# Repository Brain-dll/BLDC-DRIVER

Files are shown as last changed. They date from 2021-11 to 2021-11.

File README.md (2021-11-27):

# BLDC-DRIVER

## INTRODUCTION
BLDC-DRIVER is usually uses for driving brusless DC motor. The brusless DC motor has three input, these inputs connect to coils. Rotor of the motor has permenant magnet, 
When inputs are energized, a temporary magnetism is occurred interaction between permanent and temporary magnets poles. As half bridge and full bridge can be designed two type of 
driver. These drivers work at the same principle but there is a difference between them . Full bridge driver can connect a coil to battery and other coil to ground at the same time. 
Thus system can be more efficient. But Half bridge driver can connect just one coil to battery or ground at the same time. You can observe difference of half and full bridge driver 
designs at below picture:

**HALF BRIDGE DRIVER**



**FULL BRIDGE DRIVER**

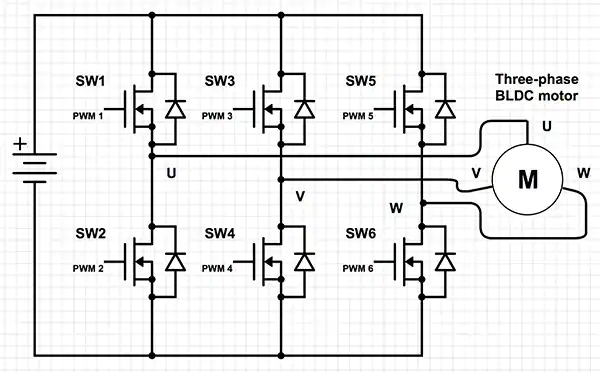
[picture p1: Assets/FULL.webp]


The problem with BLDC drivers is that they don't know the right moment of energizing. To understand when the energizing sequence changes, we must know the rotor current position firstly.
There are two way for determining current rotor position. First one is traditional technic which uses hall effect sensors. According to sensors output, driver can understand current 
moment of changing. To use extra sensors can increase motors cost, connection number and volume. So this makes our boards more complex. Second way is EMF technic. Stator coil has 
star connection, total voltage level of junction point of these coils always have to be zero. According to below picture, When rotor turns around itself total magnetic field of 
star connection be forced to stay at zero. If you observe graph of EMF and sum of magnetic fields, you can see total magnetic flux is zero. We can call common point of coils as virtual 
zero. According to EMF graph, we can understand that magnets come to middle of the two coils, when unenergized coil cross the virtual zero. Thus we can detect correct moment for 
energizing next coil. For example, when A input be charged and B input is uncharged, C input will be inducted with energy and due to motion, the pole of energy will be changed. Thus 
the energy of C input crosses the virtual zero limit. This level-changing event will be followed by the controller. When this event occurs, the ISR goes into propagation and the energizing 
order is changed.

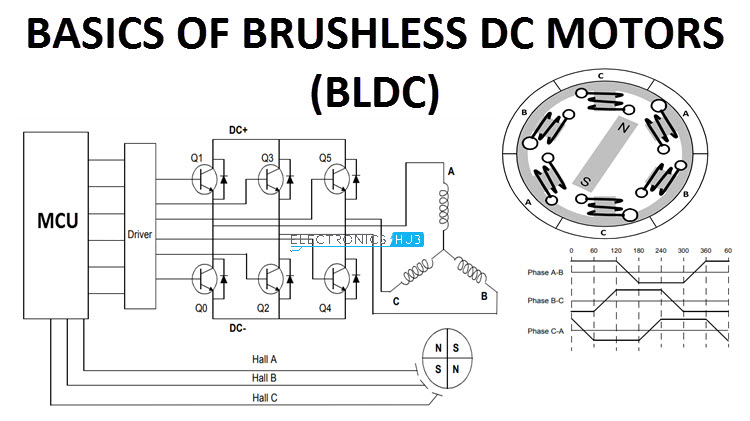
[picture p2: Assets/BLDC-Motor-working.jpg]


Above diagram show full bridge driver structure. Purpose of this project is designing our own a full bridge motor driver and developing drive algorithms at commercial driver level. 
Actually, this project is first step of the orginal drone project. This project was planned as two variant, one of them is a bit bigger than other one. Controllers of variants can 
be different and some components will be able to change. Both of variants will be produced and tested.

## ATMEGA88PA VARIANT
ATMEGA88PA is controller which was produced by microchip company. It is cheap, easily findable and It includes programmable comparator. Thanks to programmable comparator, more space 
can be earned at the board. Flash memory has less space so we can better program it without bootloader. We can earn more memory as programming at register level.

### Components

* ATMEGA88PA Controller
* TC427COA Mosfet Driver
* IRLR7843TRPBF Mosfet
* Other passive components

**Warning : Mosfet driver has to be noninverting, Inverting drivers has PMOS technology so It's working prenciple is vice versa.**

Our schematic design consist of two page. First of them includes controller design and second one includes mosfets, drivers and connectors

**First Page:**

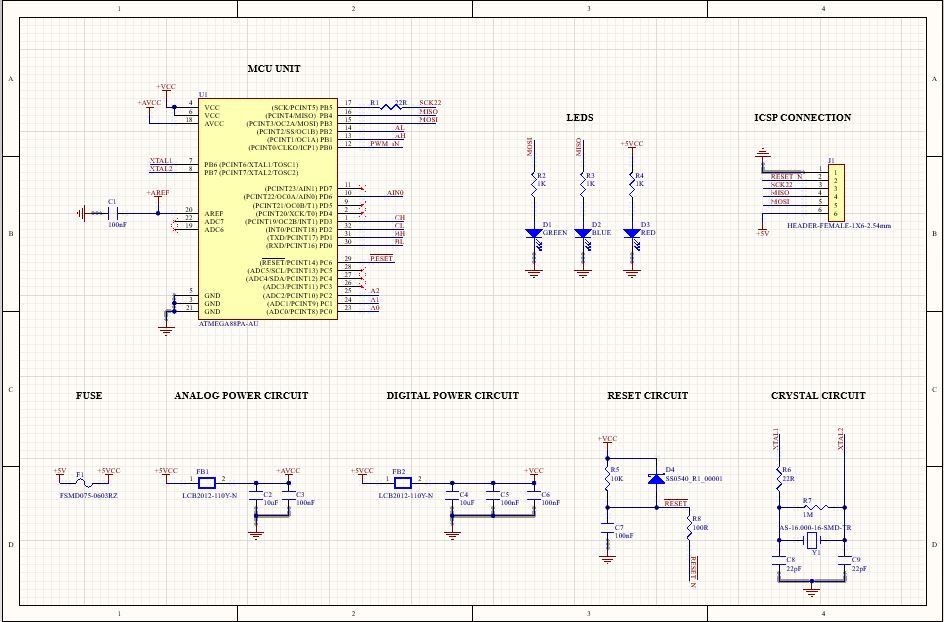
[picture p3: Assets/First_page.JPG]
First_page


**Second Page:**

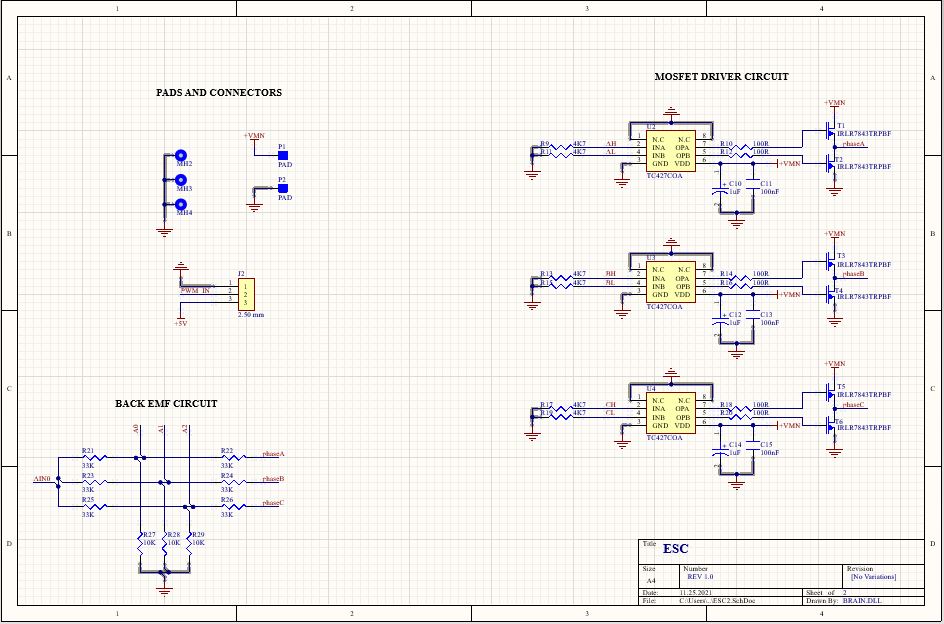
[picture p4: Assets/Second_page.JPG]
Second_page


As you can see, some resistors combination was built, purpose of this combination is taking acceptable feedback from driver (for back EMF).

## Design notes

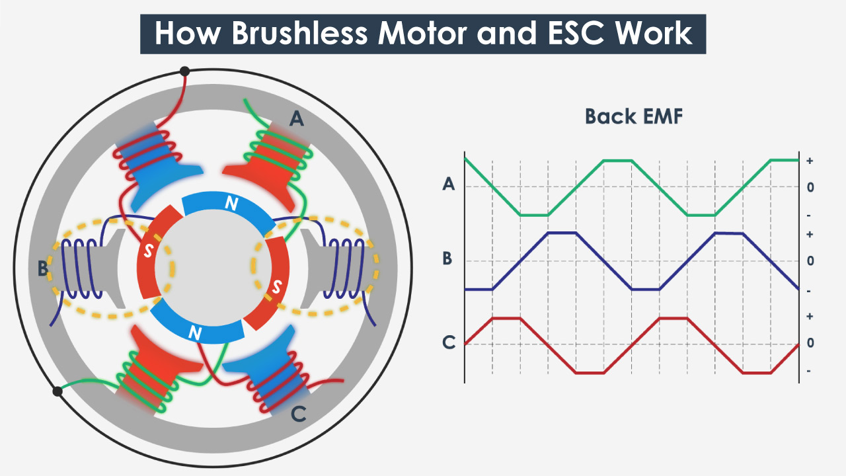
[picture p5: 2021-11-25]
Assets/ESC-Work.jpg

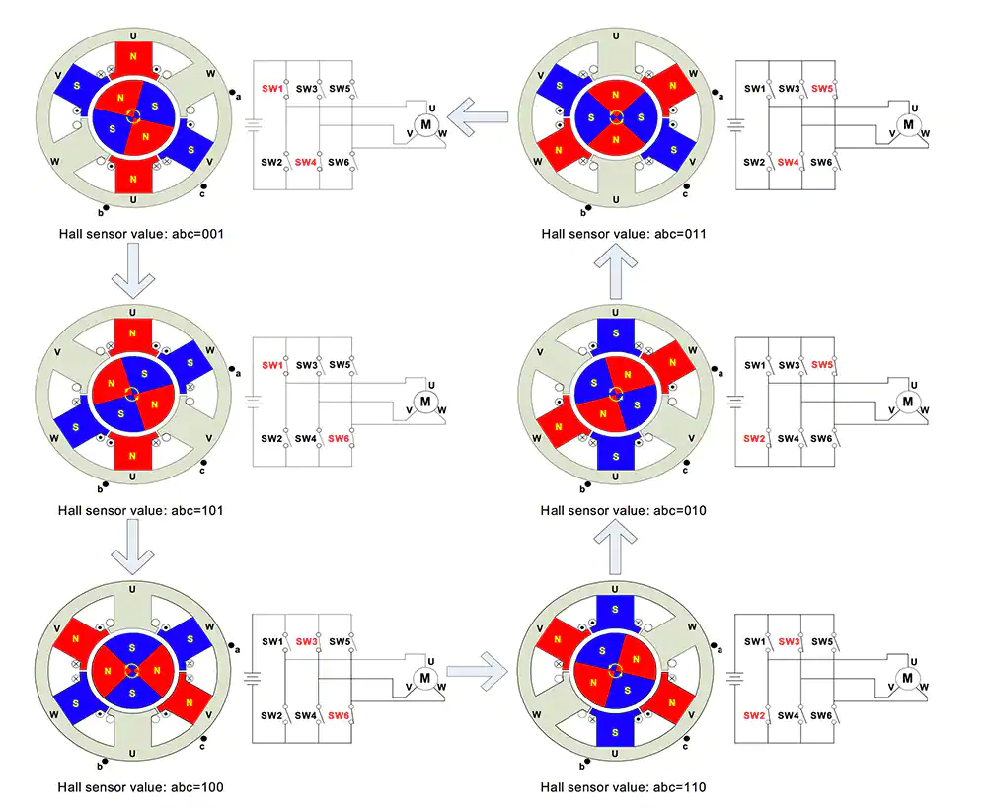
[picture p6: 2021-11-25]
Assets/BLDC_TURNING.webp

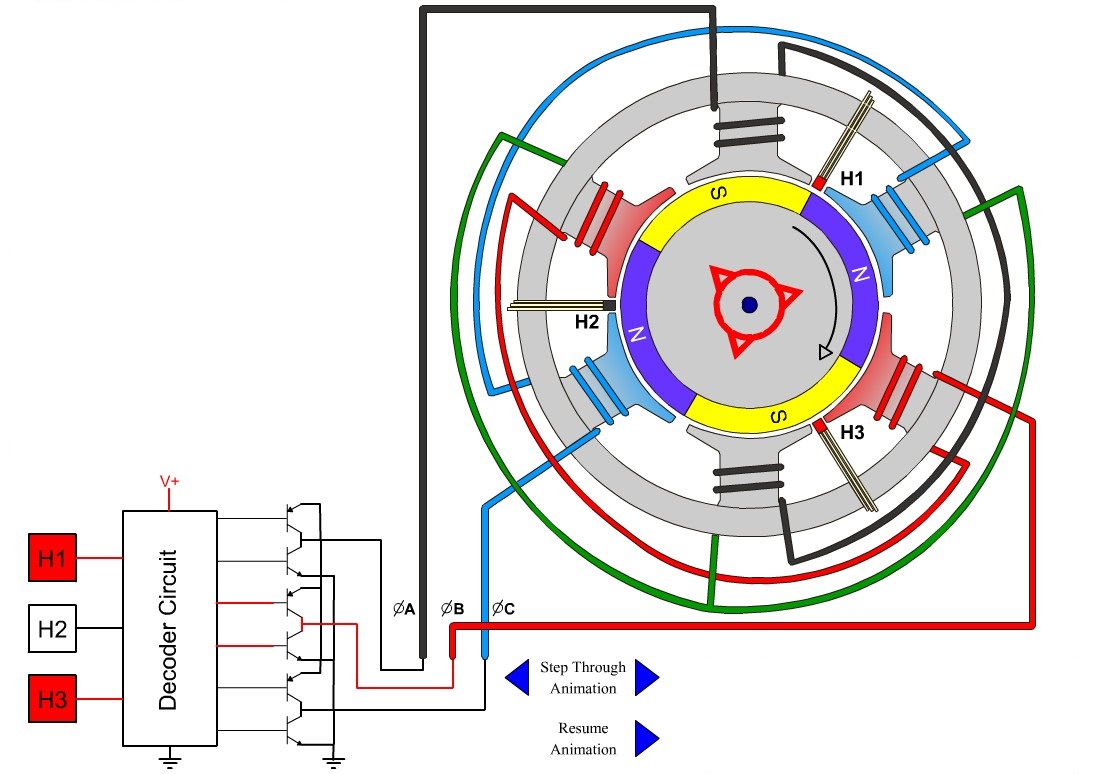
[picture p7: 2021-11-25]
Assets/DC-motor-animation.jpg

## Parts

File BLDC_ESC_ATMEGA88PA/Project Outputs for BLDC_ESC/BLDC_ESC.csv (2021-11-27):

Comment | Designator | Footprint | LibRef | Quantity | OZDISAN_PRICE | Component_Price | ComponentLink1URL
100nF | C1, C3, C5, C6, C7, C11, C13, C15 | Z0603 | CL10B104KB8NNNC | 8 | 0,05 | 0,4 | https://ozdisan.com/pasif-komponentler/kondansatorler/smt-smd-ve-mlcc-kondansatorler/CL10B104KB8NNNC
10uF | C2, C4 | Z0603 | CL10A106KP8NNNC | 2 | 0,6 | 1,2 | https://ozdisan.com/Product/Detail/350863/CL10A106KP8NNNC
22pF | C8, C9 | Z0603 | CL10C220JB8NNNC | 2 | 0,09 | 0,18 | https://ozdisan.com/pasif-komponentler/kondansatorler/smt-smd-ve-mlcc-kondansatorler/CL10C220JB8NNNC
1uF | C10, C12, C14 | 1206 TANTAL CAP | T491A105K035AT | 3 | 1,78 | 5,34 | https://ozdisan.com/pasif-komponentler/kondansatorler/tantal-kondansatorler/T491A105K035AT
GREEN | D1 | LED-0603 | HL-PST-1608U51GC | 1 | 0,22 | 0,22 | https://ozdisan.com/Product/Detail/471660/HL-PST-1608U51GC
BLUE | D2 | LED-0603 | 27-21/B7C-ZR1S1N/3C | 1 | 1,46 | 1,46 | https://ozdisan.com/led-ve-aydinlatma-cozumleri/led-komponentler/sinyal-ledler-renkli/27-21B7C-ZR1S1N3C
RED | D3 | LED-0603 | LTST-C190KRKT | 1 | 0,38 | 0,38 | https://ozdisan.com/led-ve-aydinlatma-cozumleri/led-komponentler/sinyal-ledler-renkli/LTST-C190KRKT
SS0540_R1_00001 | D4 | SOD-123 | SS0540_R1_00001 | 1 | 0,55 | 0,55 | https://ozdisan.com/guc-yari-iletkenleri/diyotlar-modul-diyotlar-ve-dogrultucular/schottky-diyotlar/SS0540R100001
FSMD075-0603RZ | F1 | F-0603 | FSMD075-0603RZ | 1 | 3,16 | 3,16 | https://ozdisan.com/guc-yari-iletkenleri/devre-koruyucu-komponentler/ptc-sigortalar/FSMD075-0603RZ
LCB2012-110Y-N | FB1, FB2 | C0805 | LCB2012-110Y-N | 2 | 0,22 | 0,44 | https://ozdisan.com/pasif-komponentler/induktorler/bead-feritler/LCB2012-110Y-N
HEADER-FEMALE-1X6-2.54mm | J1 | FEMALE-1X6-2.54MM | PPPC061LFBN-RC | 1 | 0 | 0 | https://media.digikey.com/pdf/Data%20Sheets/Sullins%20PDFs/Female_Headers.100_DS.pdf?src-supplier=Digi-Key
2.50 mm | J2 | L-KLS1-XL4-2.50-03-R | L-KLS1-XL4-2.50-03-R | 1 | 0,27 | 0,27 | https://ozdisan.com/konnektor-ve-baglanti-elemanlari/konnektor-cesitleri/pcb-konnektorler/L-KLS1-XL4-2-50-03-R
22R | R1, R6 | Z0603 | MC0603SAF220JT5E | 2 | 0,02 | 0,04 | https://ozdisan.com/pasif-komponentler/direncler/smt-smd-ve-cip-direncler/0603SAF220JT5E
1K | R2, R3, R4 | Z0603 | MC0603SAF1001T5E | 3 | 0,02 | 0,06 | https://ozdisan.com/pasif-komponentler/direncler/smt-smd-ve-cip-direncler/0603SAF1001T5E
10K | R5, R27, R28, R29 | Z0603 | CQ03SAF1002T5E | 4 | 0,03 | 0,12 | https://ozdisan.com/pasif-komponentler/direncler/smt-smd-ve-cip-direncler/CQ03SAF1002T5E
1M | R7 | Z0603 | MC0603SAF1004T5E | 1 | 0,02 | 0,02 | https://ozdisan.com/pasif-komponentler/direncler/smt-smd-ve-cip-direncler/0603SAF1004T5E
100R | R8, R10, R12, R14, R16, R18, R20 | Z0603 | 0603SAJ0101T5E | 7 | 0,02 | 0,14 | https://ozdisan.com/pasif-komponentler/direncler/smt-smd-ve-cip-direncler/0603SAJ0101T5E
4K7 | R9, R11, R13, R15, R17, R19 | Z0603 | MC0603SAF4701T5E | 6 | 0,02 | 0,12 | https://ozdisan.com/pasif-komponentler/direncler/smt-smd-ve-cip-direncler/0603SAF4701T5E
33K | R21, R22, R23, R24, R25, R26 | Z0603 | RI0603L3302FT | 6 | 0,09 | 0,54 | https://ozdisan.com/pasif-komponentler/direncler/smt-smd-ve-cip-direncler/TC0325B3302T5C
IRLR7843TRPBF | T1, T2, T3, T4, T5, T6 | TO-252-3 | IRLR7843TRPBF | 6 | 14,41 | 86,46 | https://www.ozdisan.com/guc-yari-iletkenleri/mosfetler/mosfet-discrete/IRLR7843TRPBF
ATMEGA88PA-AU | U1 | TQFP32(ATMEGA88) | ATMEGA88PA-AU | 1 | 33,63 | 33,63 | https://ozdisan.com/entegre-devreler-ics/embedded-entegreler/mikroislemciler/ATMEGA88PA-AU
TC427COA | U2, U3, U4 | SOIC-8 | TC427COA | 3 | 20,56 | 61,68 | https://ozdisan.com/entegre-devreler-ics/guc-entegreleri/guc-surucu-entegreleri/TC427COA
AS-16.000-16-SMD-TR | Y1 | AS-16.000-16-SMD-TR | AS-16.000-16-SMD-TR | 1 | 1,95 | 1,95 | https://ozdisan.com/Product/Detail/40446/AS-16-000-16-SMD-TR
 |  |  |  |  |  | 198,36

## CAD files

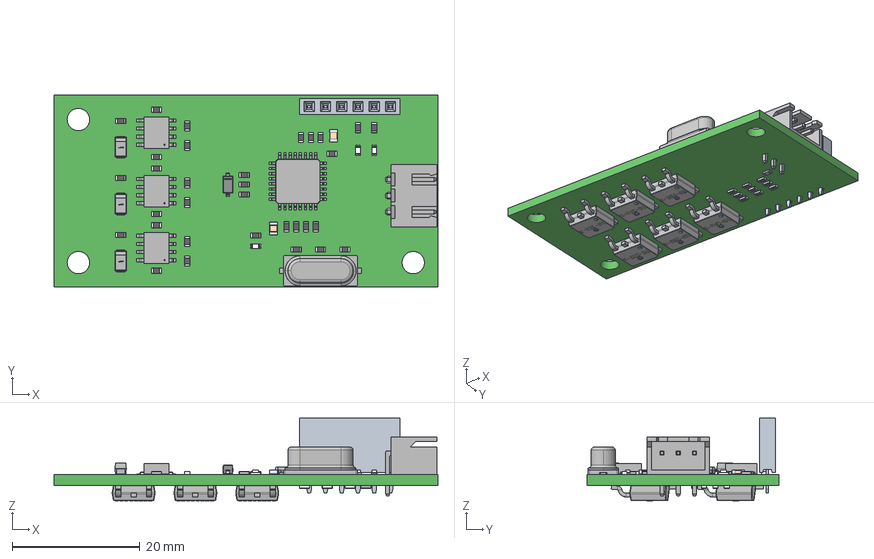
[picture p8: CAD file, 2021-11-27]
BLDC_ESC_ATMEGA88PA/Project Outputs for BLDC_ESC/ESCV2.step
60.0 x 30.0 x 12.9 mm
FEMALE-1X6-2,54mm
HC-49S_RGB8421504
SOIC8_ONS_RGB8421504 x 3
TQFP32_RGB8421504
TO-252-3_RGB8421504 x 6
Pin1Body x 42
Pin2Body x 42
CeramicBody x 42
CoatingBody x 42
JST_-_XH_-_Thru_(R)_-_3Pin_-_2.54mm_RGB8421504
C0805A x 2
SOD-123
LED_SMD0603 x 3
2012_TANTAL_KEMET_RGB8421504 x 3

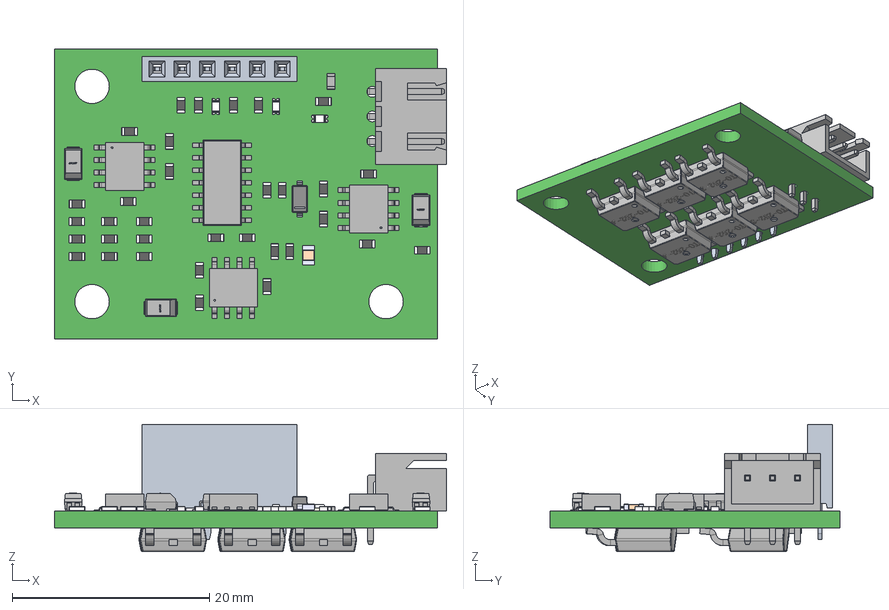
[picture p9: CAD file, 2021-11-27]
BLDC_ESC_ATTINY24A/Project Outputs for BLDC_ESC/ESCV2.step
39.8 x 29.5 x 12.9 mm
FEMALE-1X6-2,54mm
SOIC8_ONS_RGB8421504 x 3
2012_TANTAL_KEMET_RGB8421504 x 3
ATTINY24A-SSU_RGB8421504
TO-252-3_RGB8421504 x 6
Pin1Body x 34
Pin2Body x 34
CeramicBody x 34
CoatingBody x 34
JST_-_XH_-_Thru_(R)_-_3Pin_-_2.54mm_RGB8421504
C0805A
SOD-123
LED_SMD0603 x 3

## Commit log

2021-11-23 Version 2 was orginized for routing
    [BLDC_ESC.PrjPcb, ESC1.SchDoc, ESC2.SchDoc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]
2021-11-25 Components were orginized on the board file and Readme file was started to fill
    [ESC1.SchDoc, ESCLib1.PcbLib, ESCV2.PcbDoc]
2021-11-25 Variant ATMEGA88PA was completed, fabrication and report file was generated
    [BLDC_ESC.PrjPcb, BLDC_ESC.csv, ESC1.SchDoc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]
2021-11-27 ATMEGA88PA variant was completed and fabrication datas were produced
    [BLDC_ESC.PrjPcb, BLDC_ESC.csv, ESC1.SchDoc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]
2021-11-27 VARIANT ATTINY24A was completed, fabrication and report documentation was prepared. It's ready for production
    [BLDC_ESC.csv, ESC1.SchDoc, ESC2.SchDoc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]
2021-11-29 Some bugs was corrected
    [ESCV2.GBL, ESCV2.GBO, ESCV2.GBP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]
